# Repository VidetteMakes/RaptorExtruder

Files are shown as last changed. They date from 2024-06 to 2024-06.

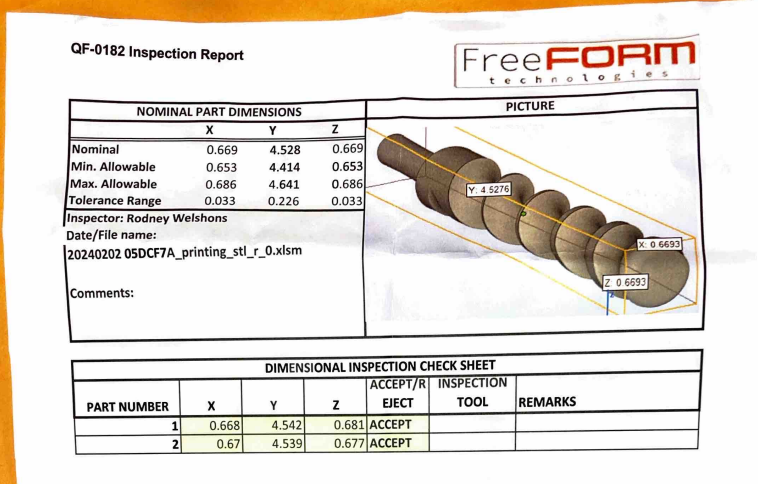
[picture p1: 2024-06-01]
CAD/Detailed/ExtrusionScrew Xometry Drawing.PNG

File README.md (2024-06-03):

# RaptorExtruder
Instructions to modify an Ender-3 3D printer to print from raw pellets

This pellet printing modification is designed to be open source, available to hobbyists for purchase and install. The pellet printer is able to bypass the manufacturing costs associated with filament printing, use flexible materials normally unsuitable for filament printing, and allow users to mix pellets for their own blends of printed material.

## Team
These fine Valparaiso University students worked for nine months to make this project happen:  [Blake Andrew](mailto:blake.andrew@valpo.edu), [Daniel Heinrich](mailto:daniel.heinrich@valpo.edu), [Mikey Pinchok](mailto:mikey.pinchok@valpo.edu), [Kay Shoolian](mailto:kay.shoolian@valpo.edu), [Ethan Storer](mailto:ethan.storer@valpo.edu), and [Timothy Ziemann](mailto:timothy.ziemann@valpo.edu).  Their team name was the "Vinyl Velocirapters."

Vidette Makes' [Adam Johnson](mailto:ajohnson@videttemakes.org) proposed the project and served as the team's "customer."

## Documentation
* [Design Document](https://github.com/VidetteMakes/RaptorExtruder/wiki/Design-Document)

## A Word from our Sponsor
Vidette Makes is a maker group in Valparaiso, Indiana, USA. We are a community of technical professionals, creatives, and enthusiasts working to build a shared workspace to enrich our city through meaningful educational and social projects. Our hope is that senior design projects like these can help improve education throughout our region, and benefit the open-source community.

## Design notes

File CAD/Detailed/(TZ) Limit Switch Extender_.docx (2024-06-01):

Timothy Ziemann

Limit Switch Extender

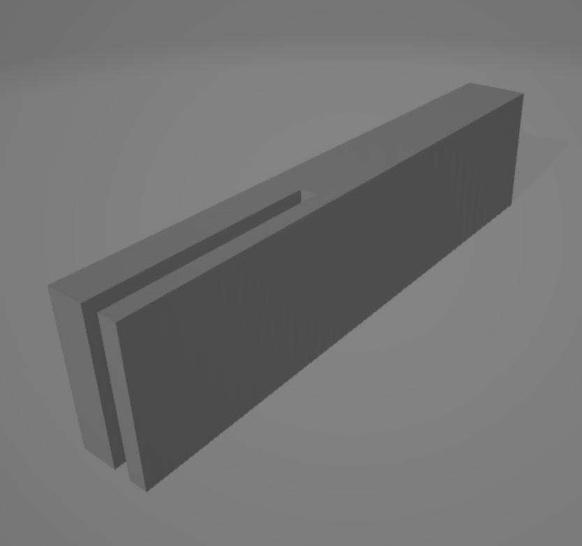
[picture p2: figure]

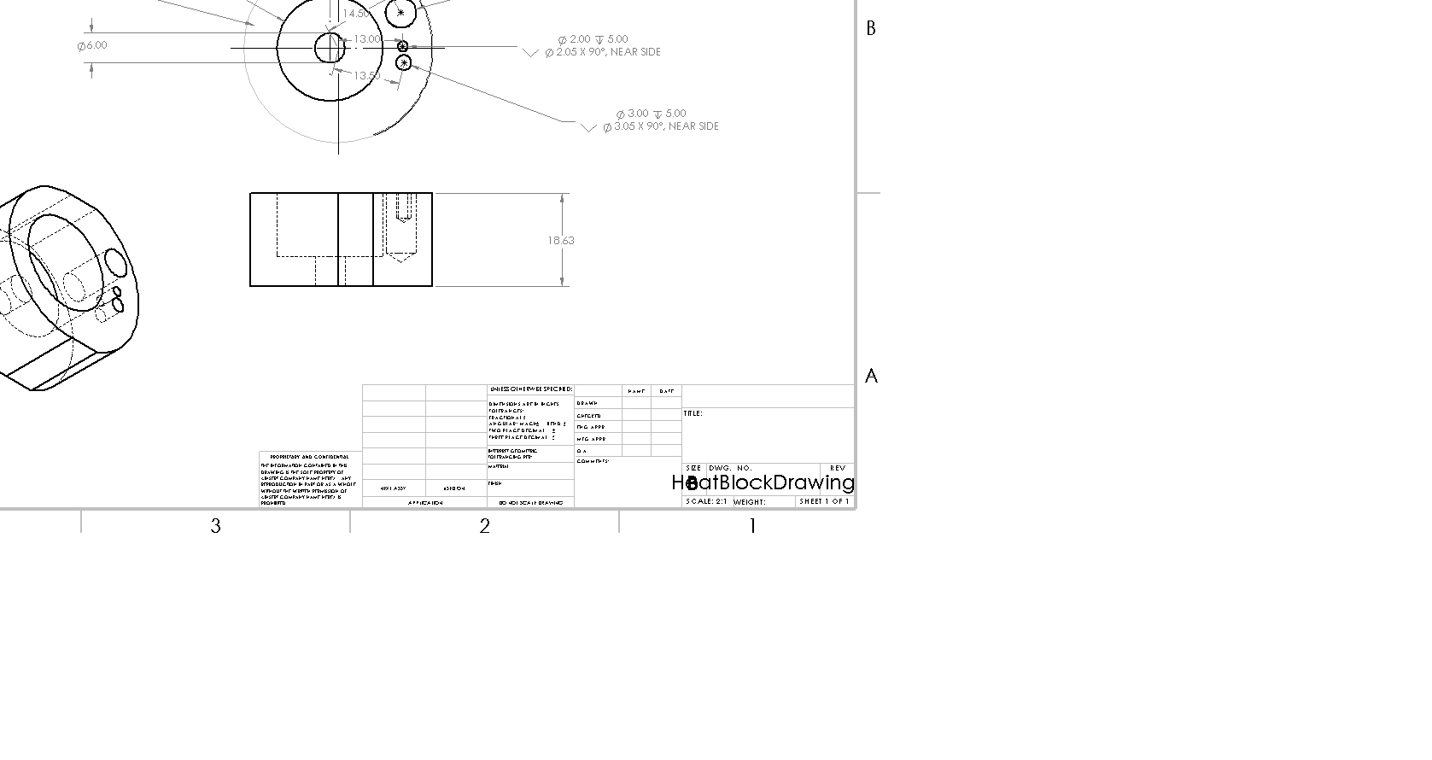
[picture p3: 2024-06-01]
CAD/Detailed/HeatBlockDrawing.JPG

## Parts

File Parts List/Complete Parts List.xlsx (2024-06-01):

Part Name | Part Number | Manufacturer | Supplier | Supplier number | Quantity | Unit per Cost | Shipping | Link | Total | 0.503902218
Central Teapot | 01 | 3D Printed | Onshape/Github Files | null | 1 | $2.82 | null | https://cad.onshape.com/documents/9373b47fd643172cff45d3d4/w/6b3f12529ad0d21ca0c2727d/e/8014758e9e8911c7f829dec0 | $196.25
Barrel Clamps | 02 | 3D Printed | Onshape/Github Files | null | 2 | $0.48 | null | https://cad.onshape.com/documents/d60d43ca9705b24c87fe40b2
Fan Bracket | 03 | 3D Printed | Onshape/Github Files | null | 1 | $0.34 | null | https://cad.onshape.com/documents/eff08e7556119b477b11b817
Extrusion Screw | 04 | Xometry | Onshape/Github Files | NA | 1 | $68.17 | FREE | https://cad.onshape.com/documents/d2be099d6e50864f19c8ab5b/w/c3f151076c51f3df40b7c22b/e/451508f13a050d7e0df22d9a
Barrel Drill Jig | 05 | 3D Printed | Onshape/Github Files | null | 1 | $0.18 | null | https://cad.onshape.com/documents/5ecc7b5bd6e7c801915e2fe7/w/c172fd17e7c9f8a495fd555d/e/54c839c322dd78154e47972e
Heat Block | 06 | Xometry | Onshape/Github Files | NA | 1 | $89.89 | FREE | https://cad.onshape.com/documents/1759477e29ceef14d57d62ff/w/edbe1dfc022f062bbb53088f/e/fbbaa3c68424f225d66270d6
Limit Switch Extension | 07 | 3D Printed | Onshape/Github Files | null | 1 | $1.83 | null | https://cad.onshape.com/documents/66e5bc53bb85858bbdae4f5e/w/fd5296b0bee12057fadcdff0/e/4f6b8865d1156799d3cb627d
O-ring Assortment (https://www.homedepot.com/p/Everbilt-Medium-Assorted-O-Ring-Kit-45-Pieces-866810/318763123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) | 08 | Everbilt | Home Depot | (219)531-6687 | 1 | $5.48 | null
Press Fit Shroud | 09 | 3D Printed | Onshape/Github Files | null | 1 | $0.08 | null | https://cad.onshape.com/documents/27f05f00ce109d2de31b7cee
1/2" x 11" Black Steel Nipple (https://www.homedepot.com/p/STZ-1-2-in-x-11-in-Black-Steel-Nipple-PDB-N12X11/316939836) | 12 | STZ | Home Depot | (219)531-6687 | 1 | $3.99 | null
8mm to 5mm coupler (https://www.amazon.com/Aluminium-Flexible-Coupling-Diameter-Connector/dp/B08JZ1D5BY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) | 85 | VI-CHAN | Amazon | null | 1 | $9.99 | FREE
Stepper Motor (https://www.amazon.com/Comgrow-Creality-Official-Stepper-Motor/dp/B09ZQT9DJY?th=1) | 00 | Creality | Amazon | 86 755 3396 5666 | 1 | $12.99 | FREE
10-32 x 3" Bolt | 10323 | null | Project Lab | null | 2 | null | null | null
10-32 x 2.5" Bolt | 103225 | null | Project Lab | null | 2 | null | null | null
10-32 x 2" Bolt | 10322 | null | Project Lab | null | 4 | null | null | null

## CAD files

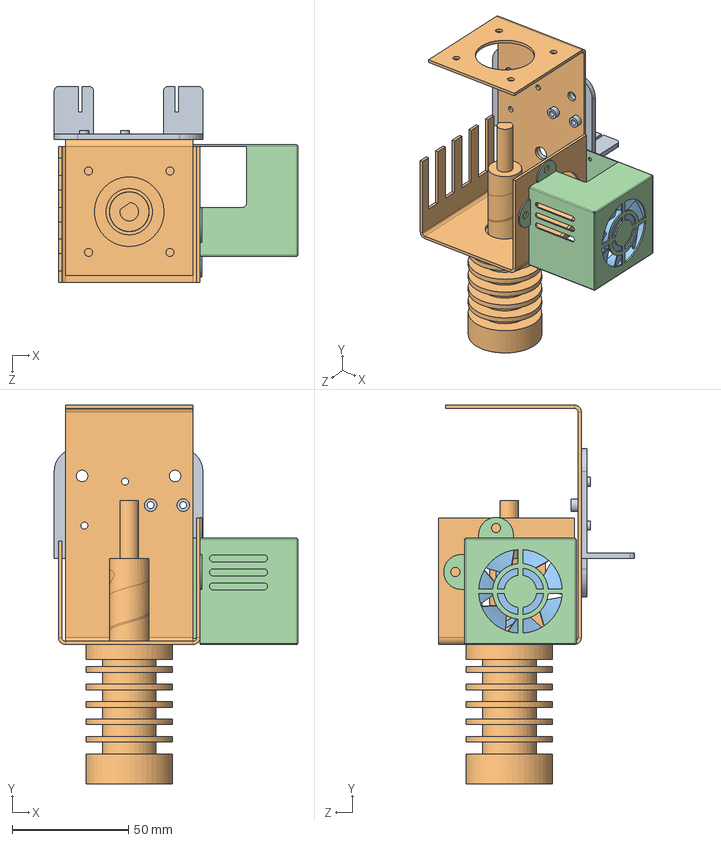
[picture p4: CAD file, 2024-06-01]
CAD/Assembly/HOTEND_ASSEM_KAY.SLDASM
104.8 x 163.0 x 84.4 mm
E plate
Storer_ExtrusionScrew x 4
Nozzle fan
Fan cover

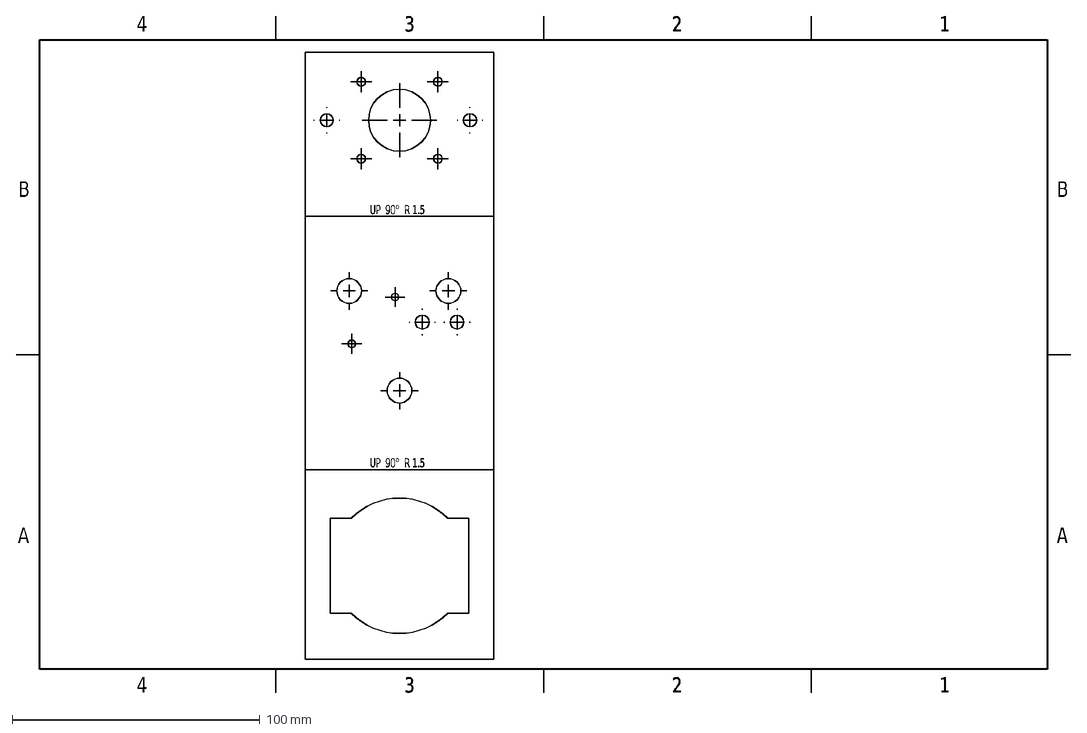
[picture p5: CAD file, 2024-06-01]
CAD/STL and DXF files/PLASMA_BRACKET_KS.DXF
A
B
4
3
2
1
UP 90° R 1.5

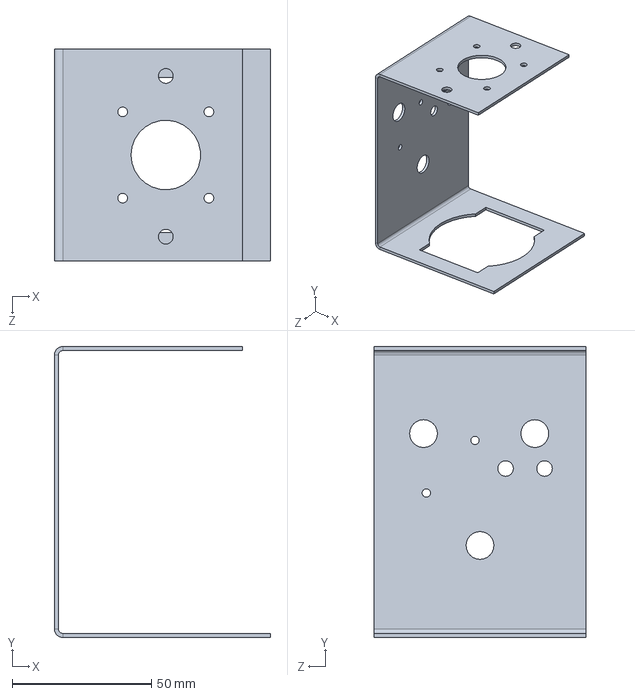
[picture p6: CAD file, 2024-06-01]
CAD/Detailed/PLASMA_BRACKET_KS.SLDPRT
77.7 x 104.6 x 76.2 mm

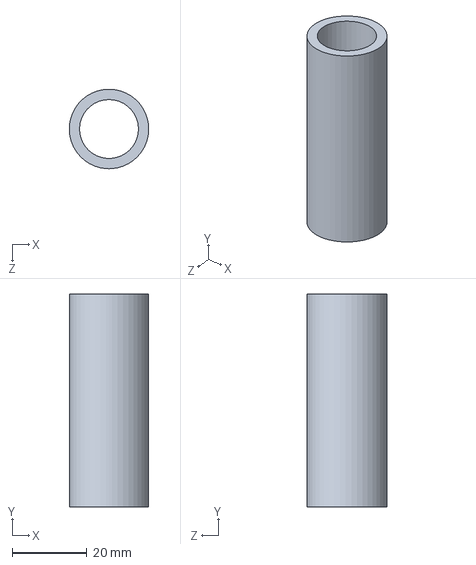
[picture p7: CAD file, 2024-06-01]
CAD/Detailed/KISS_Barrel.SLDPRT
21.3 x 57.1 x 21.3 mm

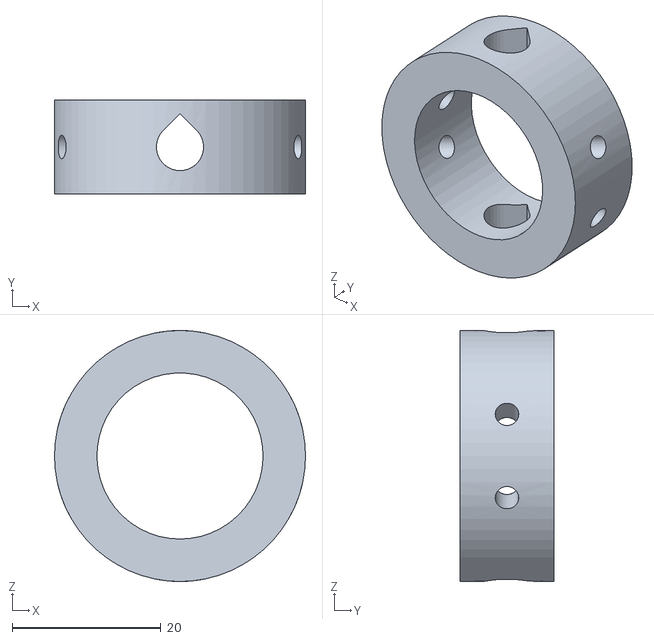
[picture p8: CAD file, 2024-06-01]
CAD/STL and DXF files/BarrelDrillJig.STL
33.8 x 12.7 x 33.8

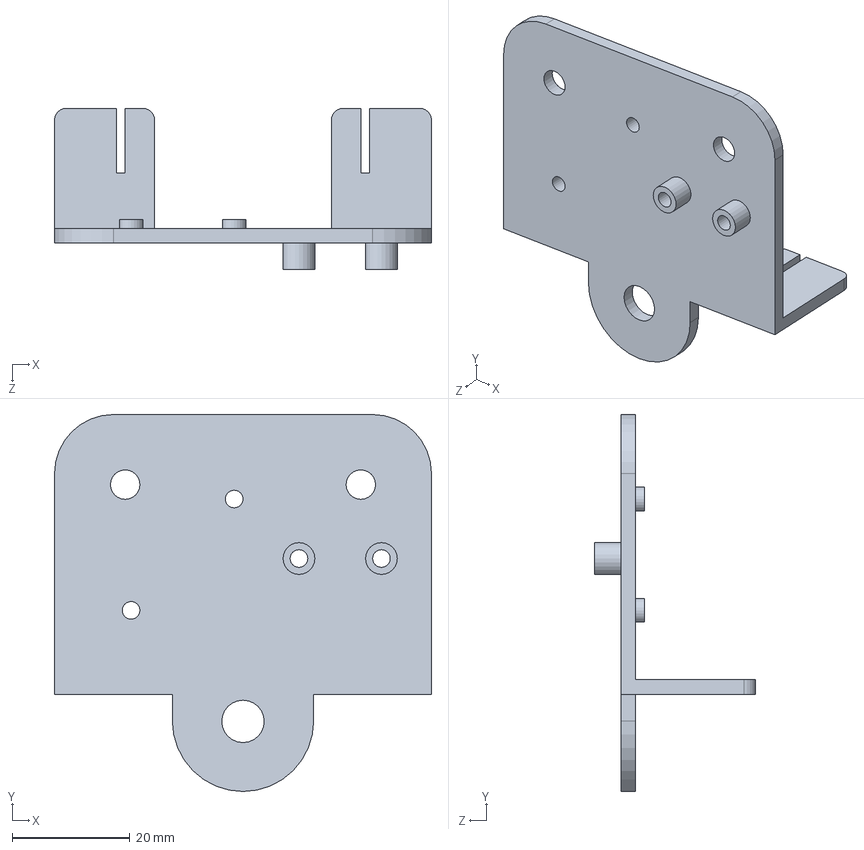
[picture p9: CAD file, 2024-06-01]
CAD/Detailed/E plate.SLDPRT
64.0 x 64.0 x 27.4 mm

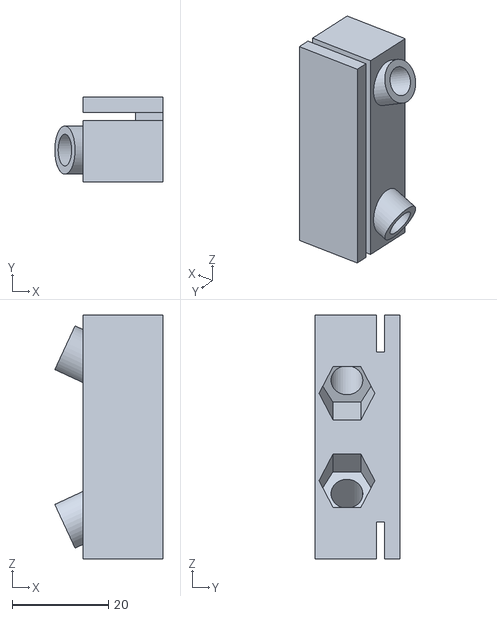
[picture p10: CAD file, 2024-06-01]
CAD/STL and DXF files/BARREL_CLAMPS_V2_KAY.STL
22.5 x 17.6 x 50.6

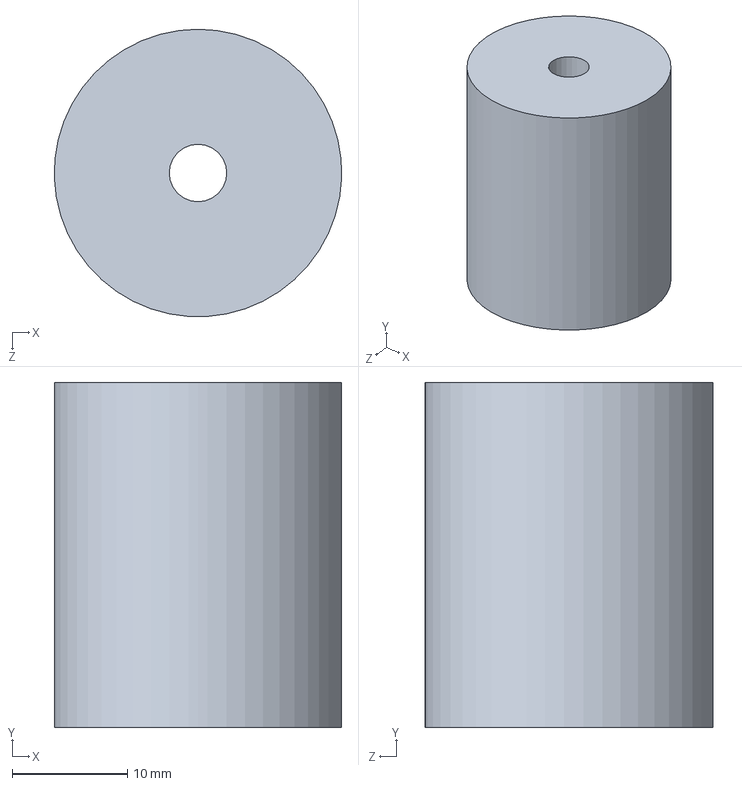
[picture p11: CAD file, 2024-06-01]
CAD/Detailed/COUPLER.SLDPRT
25.0 x 30.0 x 25.0 mm

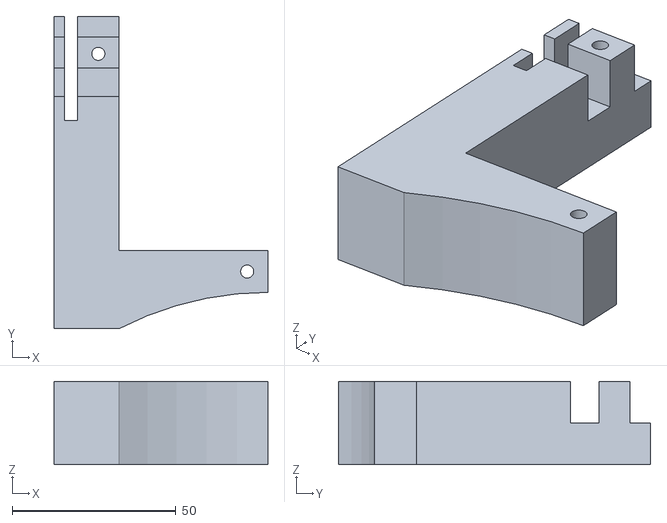
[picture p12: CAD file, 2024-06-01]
CAD/STL and DXF files/2.5in Limit Switch Extension.stl
65.3 x 95.2 x 25.4

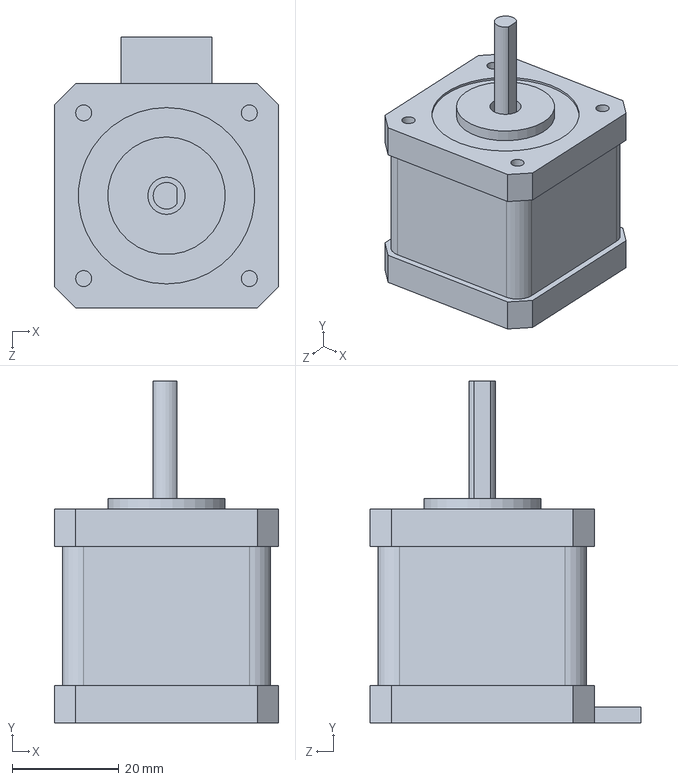
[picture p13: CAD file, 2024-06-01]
CAD/Detailed/42-40 motor.SLDPRT
42.0 x 64.0 x 50.7 mm

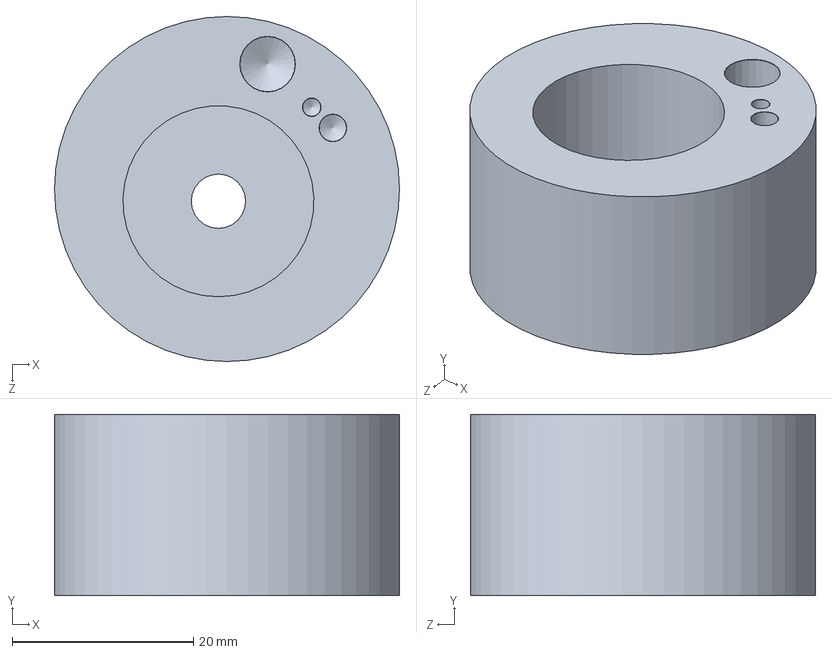
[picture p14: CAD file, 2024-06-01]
CAD/Detailed/Heat Block.SLDPRT
38.1 x 20.0 x 38.1 mm

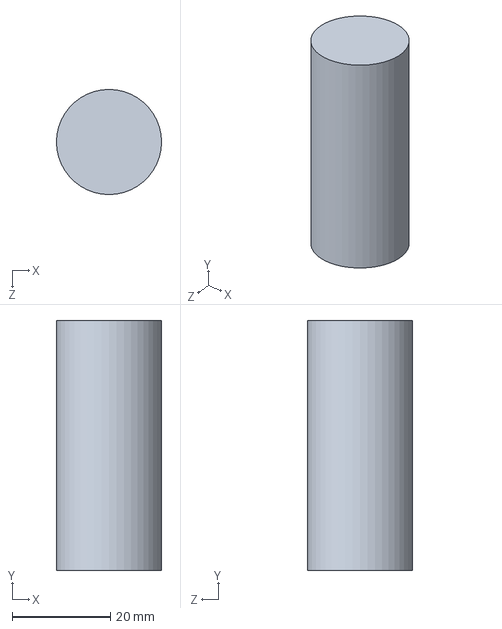
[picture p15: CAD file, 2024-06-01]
CAD/Detailed/SIMPLE_BARREL.SLDPRT
21.4 x 50.8 x 21.4 mm

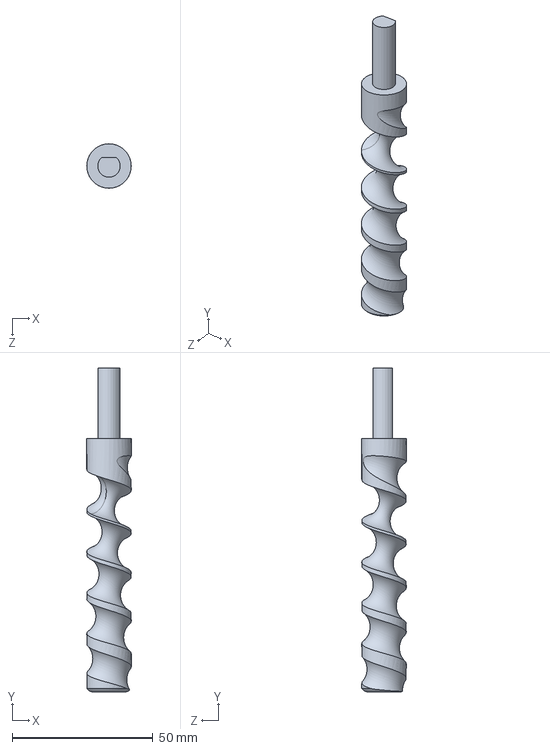
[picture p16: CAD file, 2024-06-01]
CAD/Detailed/Storer_ExtrusionScrew_TurnedDownV2.SLDPRT
15.8 x 115.0 x 15.8 mm

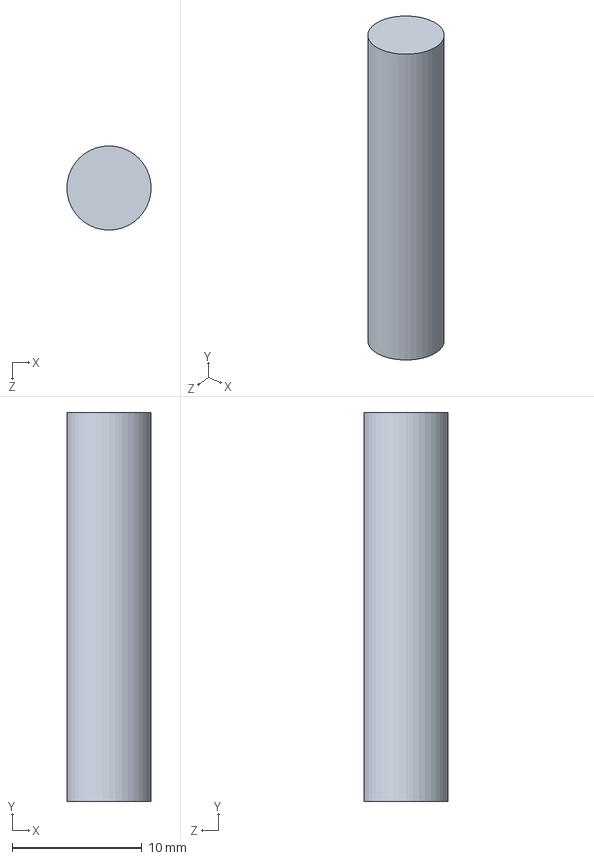
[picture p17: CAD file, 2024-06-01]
CAD/Detailed/TEST_SCREW.SLDPRT
6.50 x 30.0 x 6.50 mm

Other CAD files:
CAD/Detailed/BARREL_CLAMPS_V2_KAY.SLDPRT
CAD/Drawings/Heat Block.SLDDRW
CAD/Drawings/PLASMA_BRACKET_KS.SLDDRW

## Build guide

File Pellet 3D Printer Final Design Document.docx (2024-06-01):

Multidisciplinary Senior Design Projects

GE 498

College of Engineering

Valparaiso University

Valparaiso, Indiana

Design Document

For the

Pellet 3D Printer

Date: 05-06-2024

Prepared by: | Pellet 3D Printing (Vinyl Velociraptors)
Concurrence (Advisor): | Professor Luke
Concurrence (Advisor): | Professor El-Howayek
Approved (Customer):
Approved (Team Leader):

Total Number of Pages: 15

Executive Summary: This pellet printing modification is designed to be open source, available to hobbyists for purchase and install. The pellet printer is able to bypass the manufacturing costs associated with filament printing, use flexible materials normally unsuitable for filament printing, and allow users to mix pellets for their own blends of printed material.

Honor Code Statement

I have neither given or received, nor have I tolerated other’s use of unauthorized aid.

_________________________________________

Blake Andrew

_________________________________________

Daniel Heinrich

_________________________________________

Mikey Pinchok

_________________________________________

Kay Shoolian

_________________________________________

Ethan Storer

_________________________________________

Timothy Ziemann

Table of Contents

1 Introduction 4

2 System Description 4

2.1 Subsystem Description 4

3 Frequently Asked Questions (FAQ) 5

4 Design Problems and Solutions: 6

Likely Problems while Assembling the Extruder 6

5 Limitations and warnings 6

Warnings: 7

Limitations: 7

6 System Design Requirements 8

Using An Ender-3 Requirement 8

Assembly Instructions Requirements 8

Time Study Requirements 8

Performance Check Requirements 8

Size Requirements 8

Accessibility Requirements 9

6.2 Deviations from the System Design Requirements 9

7 Supporting Information 9

7.1 Referenced Documents 10

7.2 Symbols and Abbreviations 10

8 Distribution 10

Appendix A 11

Part List and Budget: 11

Appendix D, E, F 11

Detailed drawings illustrating for all manufactured components 11

Assembly drawings: 13

Flow Charts for Control Systems 14

Computer Code: 14

Electrical circuits: 14

Appendix G 15

## 1 Introduction

The goal of this project is to modify a stock Ender-3 3D printer to accept plastic pellets rather than filament and provide detailed documentation for hobbyists who want to replicate the design change.

## 2 System Description

Our system is a modified Ender 3 3D V1 printer. It is modified to utilize plastic pellets as a printing material instead of plastic filament. This modification would make the 3D print more environmentally friendly and cheaper with use of pellets over processed filament rolls. The other main goal is to make this project and modification open source. This will provide repeatable instructions for hobbyists to modify their printers at home through following an assembly guide with steps, parts, and a time study. This design report aims to walk through our problem definition, system overview, virtual prototype, and finalized budget. Our team (The Vinyl Velociraptors) have been working on these four categories for the last 10 months and this document will be a compilation of the data and product we have made.

## 2.1 Subsystem Description

The system begins with a hopper connected to the central mounting teapot via a corrugated tube. It is mounted atop the Ender 3 V2’s gantry.

The central mounting teapot houses the barrel, hotend, fans, extrusion screw, and the stepper motor that turns the extrusion screw. It is printed on the stock Ender 3 3D printer. This component also houses the barrel mounting system. There are two 3D printed barrel clamps which secure the barrel and allow for precise adjustment of it. These can be printed by the unmodified 3D printer. The part fan and barrel fan are also a part of this system and are crucial to keeping the system at the proper temperature.

The extrusion screw utilizes a logarithmic design to build pressure to push out plastic for printing. It is purchased from Xometry.

The barrel is a pipe that can be purchased from a hardware store. It is cut to size and press fit into the heater block using a vice.

The hot end contains the heat stock Ender 3 heat cartridge, chosen for its ease of implementation and compatibility with the existing Ender 3 heat cartridge and thermistor which are also utilized for our system. This heater block also contains a 0.6mm nozzle which can be purchased from Creality. The hotend and barrel subsystem is crucial for transforming pellets into molten material, ready for extrusion through the nozzle.

A extrusion screw bit, inserted into the hotend barrel, is driven by a stepper motor. This motor has a built in 5:1 gearbox and is connected to the extrusion screw bit through a coupler. The extrusion screw and geared stepper motor ensures a controlled and consistent feeding of pellets into the hotend barrel, contributing to the overall accuracy and reliability of the 3D printing process.

The system is seamlessly integrated with the Ender 3 V2's software, allowing users to control the pellet feeding process, temperature settings, and other parameters. Ender software integration ensures user-friendly control of the 3D printing process, making it accessible to experienced and novice users.

## 3 Frequently Asked Questions (FAQ)

Q: What is the estimated cost of making this printer modification?

A: Assuming you don’t have access to a machine shop, the total comes out to be around $200

Q: Where can I buy plastic pellets?

A: Pellets can be purchased in bulk from online stores like 3DxTech, we got our polypropylene (PP) pellets from techkits.com (https://www.techkits.com/products/resin-ppnat/) because it was a much smaller quantity.

Q: How much does using pellets save compared to filament?

A: Pellets can be around 50% cheaper compared to filament. Depends on the quality of the filament and the size of the pellet order.

Q: Does this work with new versions of the Ender 3D printer?

A: Theoretically yes, although the mounting holes may be different. Nothing involved in the printing process is tied to the Ender-3 V1 specifically.

Q: How fast can this printer modification print?

A: We set it to print at 6.5mm/s for testing purposes, but likely could have printed faster. A lot of the speed limitations came down to the extra weight of the modified extruder.

Q: What slicer software did you use to make the custom settings for the pellet printer?

A: Prusa Slicer is our slicer of choice, but it is by no means the only option.

## 4 Design Problems and Solutions:

- Partially melted plastic pellets leaking through the o-ring at the interface of the “teapot” and the barrel
  - Solution was to improve the installation of the o-ring and install a new/better teapot. O-ring no longer acts as a thermal bridge
- Teapot would become partially melted the longer the printer remained hot.
  - O-ring was installed better and no longer acts as a thermal bridge
  - An additional fan was added to provide convection cooling to the top of the barrel
- Pressure created by screw during operation would deform the bracket
  - Bracket was replaced with a 3D printed teapot to provide improved rigidity.
- Screws that adjust the barrel position in the bracket do not provide adequate pressure to hold it in place.
  - Shallow blind holes can be drilled into the barrel to allow for better hold.

### Likely Problems while Assembling the Extruder

- Printer is beeping loudly
  - Thermistor is likely improperly installed or damaged. Inspect the thermistor and reseat it. If the printer continues to beep, ensure that none of the fans are blowing on it directly. If none of these fixes the beeping, consider replacing the thermistor. Also consider adding Kapton Tape (https://www.amazon.com/ELEGOO-Polyimide-Temperature-Resistant-Multi-Sized/dp/B072Z92QZ2?hvadid=616931741728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) around the heat block for improved installation. Another option to insulate the barrel if the Kapton Tape is not sufficient is the use of fiberglass insulation, like that from exhaust wrap.
- 3D prints are messy
  - Ensure you are using the provided print configurations.
- 3D prints won’t stick to the bed
  - Ensure your bed is hot enough for your choice of plastic.
  - Clean the bed using isopropyl alcohol to ensure there is no plastic residue.
  - If using Polypropylene, ensure that the bed is covered in packing tape, and that the bed heat is upwards of 80 degrees celsius.
- Packing tape is lifting off of the bed
  - While still printing, tape down the lifting sections with more packing tape

## 5 Limitations and warnings

- While using the teapot in either PETG or ABS materials, the teapot will melt if it is not set to the proper temperature and cooling levels.
  - If this becomes a constant issue, a teapot printed from a higher temperature glass transition point material such as Nylon 11 in an SLS printer can negate those problems
  - An insulative fiberglass board cut to add insulation below the teapot can reduce the heat transfer into the teapot.
    - Cheaply by hand and stencil with a pre purchased board
    - Using a laser cutting service such as sendcutsend
- While the printer is believed to be capable of printing in materials other than polypropylene, this has not been officially tested
  - Be aware of the temperature of both the teapot and especially the barrel brackets to ensure all components remain solid

### Warnings:

- Printer gets very hot, do not touch it during operation. Furthermore, ensure no flammable materials are near the printer while operating.
- Inspect your thermistor before installation to ensure that it is working properly. This reduces the risk of thermal runaway.
- It is not recommended to run a 3D printer without a person nearby in case something goes wrong
- Modify your printer at your own risk, we cannot guarantee the safety of any modifications done to the printer.
- Print in a well ventilated area to reduce the risk of toxic gasses building up, especially while using plastics like ABS or TPU

### Limitations:

- Printer cannot retract plastic while printing, leading to extra strings in the print while z-hopping.
- We don’t have an efficient way to purge old plastic while changing materials or colors
- The build height of the printer has been reduced by the increased size of the pellet extruder system.
- The print speed of the printer has been reduced by the increased weight of the pellet extruder system.
- The printer has a very limited maximum temperature of about 210°C - 220 °C. The firmware expects to see a certain amount of temperature change for some amount of power that gets dumped into the heat block. Since the heat block is much larger than the stock Ender-3 block, or any other heat block out there, it loses heat very quickly and trips the “Heating Failed” error very easily. Note that hotter temperatures will cause the printer to bleed off heat more quickly!

## 6 System Design Requirements

### Using An Ender-3 Requirement

1.1 The system shall modify an existing Ender-3 3D printer

1.2 The system shall use PP pellets instead of filament to create 3D printed objects.

1.3 The system may accept ABS, PLA, PETG and TPU pellets instead of filament.

1.4 The system shall not interfere with the safety features of the Ender-3.

### Assembly Instructions Requirements

2.1 The instructions shall describe the requirements to install the pellet modification.

2.2 The instructions shall be a highschool graduate reading level.

2.3 The instructions shall include pictures with a step by step format for building the device.

### Time Study Requirements

3.1 The construction process shall be documented and completed 3 times.

3.2 The system shall take less than 5 hours to construct for an individual who is not familiar with the design.

### Performance Check Requirements

4.1 There shall be no more than a ±5% difference in dimensions between a calibration cube printed by the system and a stock Ender-3.

4.2 There shall be no more than a ±5% difference in weight of a calibration cube printed by the system and a stock Ender-3.

### Size Requirements

5.1 The system shall fit in a 3 ft by 3 ft by 3ft cube space.

5.2 The extruder system shall weigh less than 3 pounds

### Accessibility Requirements

6.1 The system shall use widely available or simple pre-designed parts.

6.2 The materials necessary to make the modification shall cost less than $350.

6.3 The system shall avoid melting/grinding/cutting to make parts fit.

6.4 The system shall only use tools that most hobbyists have easy access to.

6.5 If there is a specialty item, its place of purchase shall be documented.

6.6 The system shall use fasteners, not glue.

6.7 The system shall use connectors whenever possible, not solder, to minimize failure of electronic components.

6.8 Any part requiring special skills (welding, soldering, or machining) to construct or assemble shall be quoted from at least three vendors, and justified by the team in a meeting to ensure it fits within the total budget.

## 6.2 Deviations from the System Design Requirements

4.1 The dimensional deviations between the stock Ender and our modification was on average ±8%

4.2 The polypropylene material we used for pellet printing is unavailable in filament form, meaning we were unable to test this requirement.

6.1 The core of the system uses a custom metal 3D printed logarithmic screw, which is neither simple nor widely available.

6.4 Some parts of the system such as the heater block had to be machined.

## 7 Supporting Information

### 7.1 Referenced Documents

US20160347000A1.pdf (https://drive.google.com/file/d/1btAa_Q-sDPHqLyyBR-ihErtMZL8ppcnh/view?usp=drive_link)

polymers-13-03353.pdf (https://drive.google.com/file/d/1Sh1UzTP04CTPRqTO__MObnyoIkQHghQI/view?usp=drive_link)

s40964-019-00088-4.pdf (https://drive.google.com/file/d/16hsIs7RPbFy4fzcSIrZV6rPczBE_E7Sp/view?usp=drive_link)

### 7.2 Symbols and Abbreviations

ABS - Acrylonitrile Butadiene Styrene

TPU - Thermoplastic polyurethane

PP - Polypropylene

## 8 Distribution

Original.......... Team Leader
1 copy............. Primary Advisor
1 copy............. Course Coordinator

## Appendix A

### Part List and Budget:

- Complete Parts List (https://docs.google.com/spreadsheets/d/110W6ZweZZwfarbQIxILViImiIQHg95aWJ4IGoY0l1n8/edit)

## Appendix D, E, F

### Detailed drawings illustrating for all manufactured components

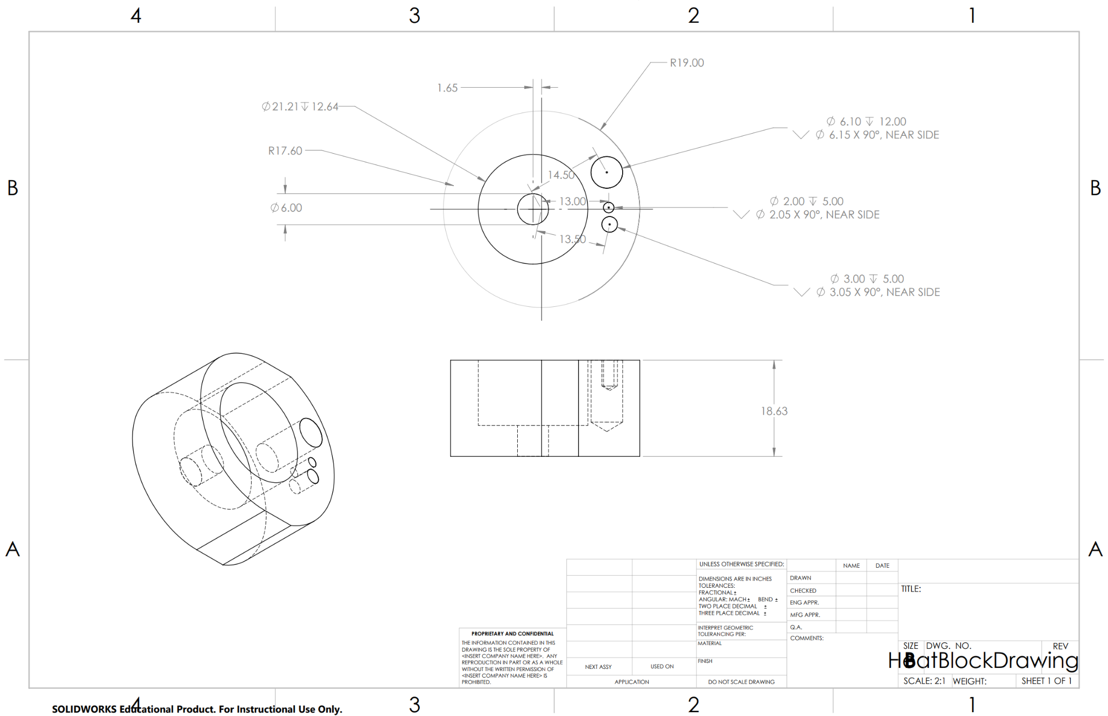
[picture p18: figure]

The flat edges are not necessary in the final design as they were originally meant for making the part more manufacturable. The barrel’s most important dimension is the press-fit hole for the black steel barrel. The dimensions for the three smaller holes follow the hole pattern spacing for the Ender-3 heat block very closely.

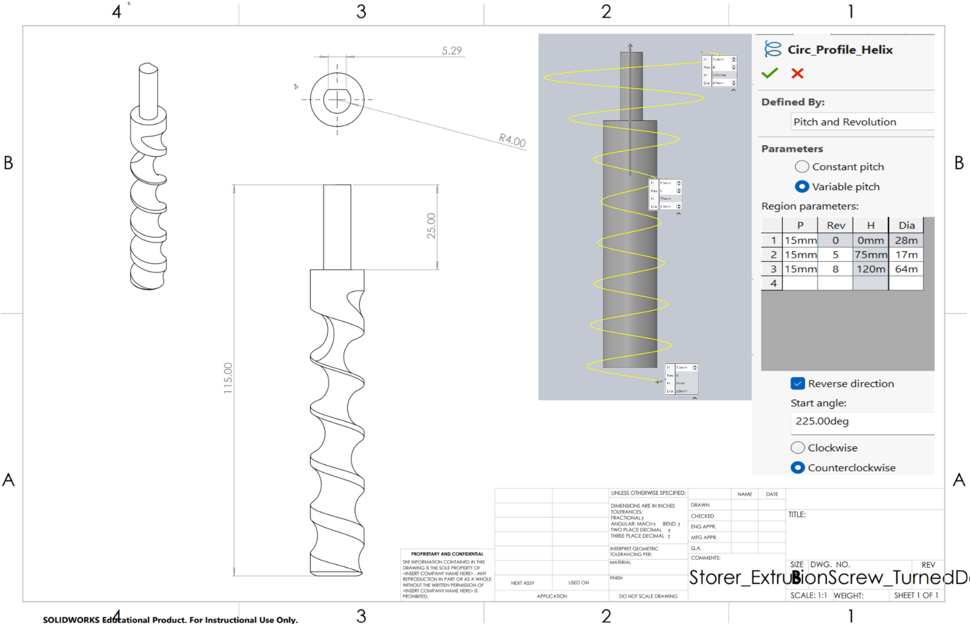
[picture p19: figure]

The screw’s geometry is based on a helix with three individual segments with their own pitch. The parameters for the helices are labeled on the preview with three little boxes. The parameters for the helices are also in the Circ_Profile_Helix table.

### Assembly drawings:

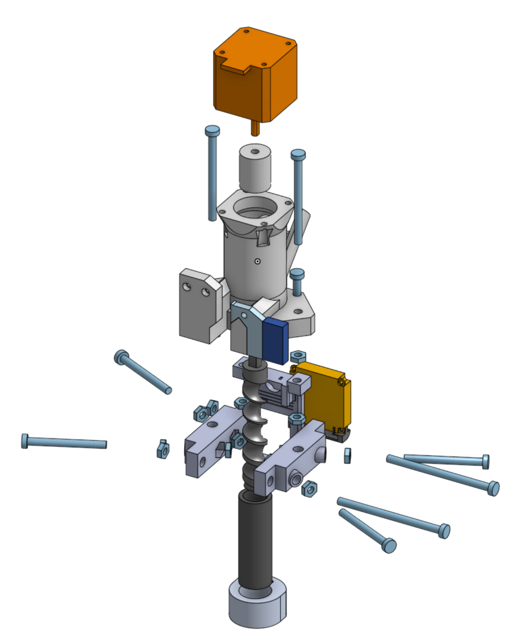
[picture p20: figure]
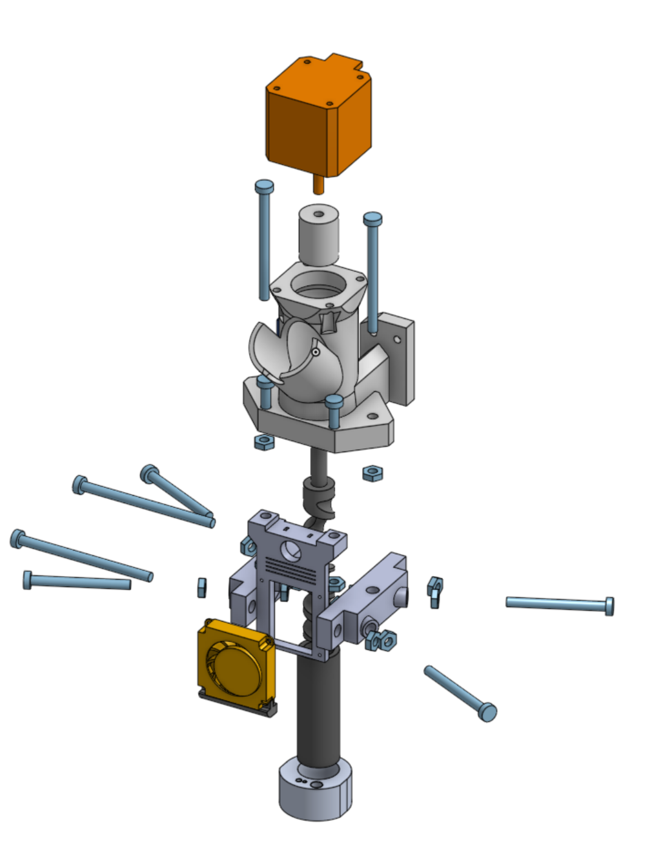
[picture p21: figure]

Two isometric views of the exploded model. The model and its parts can be found in the OnShape Project Folder (https://cad.onshape.com/documents/24ec814f0aa771ba6b6b39f4/w/7c7ef0db674f39f2ce4eb73b/e/5d7ee87e87f6b38be38cb68a).

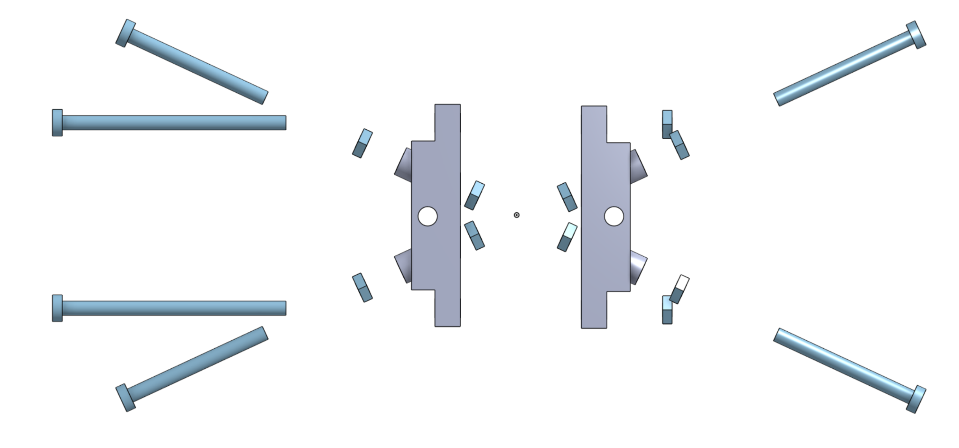
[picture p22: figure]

Isolated view of the barrel clamps and the bolts.

### Flow Charts for Control Systems

- We did not write our own control systems since the Ender 3 had built in control systems.

### Computer Code:

- We did not write code for the operation of the system, but did write code to calculate the dimensions of the screw. Those calculations are linked below.
  - Computer Codes (https://drive.google.com/drive/folders/1YNIQtn1I4rh5Mel5AXPEYvcBOearV0iV?usp=drive_link)

### Electrical circuits:

- The electrical circuits included in the Ender 3 are shown below. Besides that, we did not design any electrical circuits as the ender had all the control systems required.
  - Circuit Diagrams (https://drive.google.com/drive/folders/1OTnrep8ZZs7Rkf0-R4wiGuxogoQwrrbr?usp=drive_link)
  - The Ender Circuit provides all the control circuitry for powering the fans and sending signals to the stepper motors.
  - The stepper motor circuitry was used for our project specifically to reverse the direction of the stepper motor rotation. Such circuitry won’t be needed for future iterations of this design, as the screw will be designed correctly to extrude while spinning in the default Ender 3 “forward” direction.

## Appendix G

Pellet 3D Printer Assembly Instructions (https://docs.google.com/document/d/1HU0jos_mn8zzjRmjtwaB9pEYKUADIomTM53ebHeet08/edit)

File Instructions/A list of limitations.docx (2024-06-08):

A list of limitations

1. What materials can you print with?

We have only printed with polypropylene, however it should be possible to print with other materials such as PLA or ABS. Printing with PETG pellets might be difficult since all the 3D printed parts are made out of PETG. The customer should try materials with a lower melting temperature lower than PETG’s before experimenting with PETG pellets.

2. What print speed can you use?

Here is ai list of adjusted settings that we were able to adjust in the Ender 3 panel.

- Speed: 100 → 65
- Acceleration: 500 → 375
- Jerk VX and VY: 8 → 6
- Fan Speed: 5%

The print speed is significantly slower than a stock Ender 3. A stepper motor with agearbox could result in faster sprint speeds.

3. What flow rate can you use?

The flow was also adjusted in the panel from 100 → 50. This setting changes how fast the extruder spins when extruding. It was necessary to lower the flower, in order to achieve more torque since our stepper motor doesn’t have gearbox. However, the lowered flow doesn’t affect the printing speed by much since the extrusion screw creates an immense amount of pressure

4. What are the capabilities of the printer?

Presenting a benchy shows that the pellet 3D printer is capable of even complex geometries. The accuracy has to be improved but we showed that retraction is possible. The retraction speed must be lowered in the slicer settings however.

5. Duration of a print?

Due to lowered print speeds, the duration of a benchy print was roughly doubled from around 1.5 hours to 3 hours. Hence, expect roughly a doubled print time.

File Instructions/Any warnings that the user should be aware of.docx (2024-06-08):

Any warnings that the user should be aware of

1. Heat
  a. As with any other 3D printer, the hot end will have some very hot components. Our design includes a much larger heater block, which can be even more dangerous. Never touch the metal components until the printer is thoroughly cooled down.
  b. In our current design, we are using the extruder stepper motor to spin our extrusion screw. We recommend a stepper motor with a gearbox for future iterations since the current stepper motor can get extremely hot during a print longer than an hour or two.
2. Longevity
  a. We only extruded polypropylene with a relatively low melting temperature during our testing processes. Thus, printing with PLA or PETG pellets, which require a hotter heater block, can cause the 3D-printed parts to melt. If you see parts such as the teapot and clamps melting, turn off the printer immediately and reprint the parts. To prevent further melting the fan speeds must be adjusted accordingly.
3. Gloves and masks are necessary when working with fiberglass.
  a. When insulation is necessary, it is essential to wear gloves and masks when working with fiberglass and, ideally, work in open spaces. Keep it away from children and handle it with care.

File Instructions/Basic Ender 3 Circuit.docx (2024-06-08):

Creality Ender-3 V2 3D printer

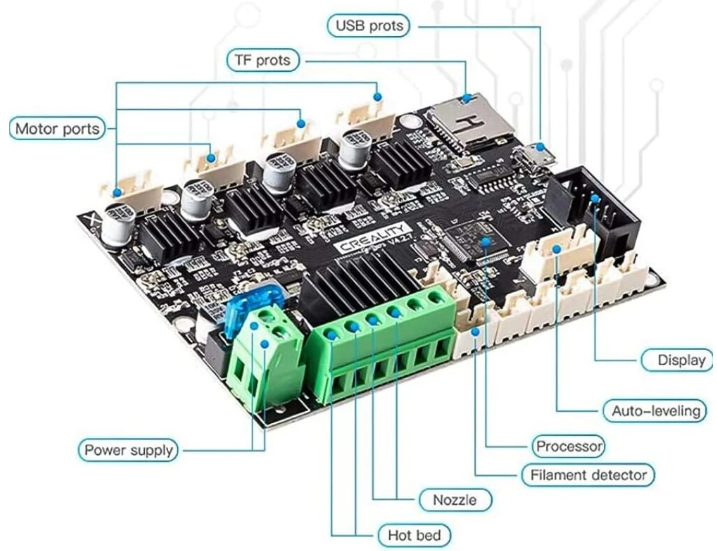
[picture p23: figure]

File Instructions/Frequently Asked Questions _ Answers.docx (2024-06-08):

Frequently Asked Questions / Answers

1. Why is a pellet 3D printer better?

Printing out of pellets is more environmentally friendly and cheaper since the extrusion process to make filament is skipped.

2. How long would it take to modify my printer?

Modifying your printer is a breeze. If you print all 3D parts overnight and deliver custom-machined parts, you can expect to have your modification assembled in just an afternoon. It's a quick and efficient process that puts you in control of your 3D printing setup.

3. What was the biggest struggle in designing the system?

Heat management thermal runaway was a significant issue during our design process. Isolating the thermistor with glass fiber solved that problem.

4. How many of the parts are custom vs off the shelf?

Even though our design ended up with more custom parts than off-the-shelf parts, our custom parts are easily accessible by providing necessary STL and CAD files. The ½ inch steel pipe is the only off-the-shelf part of our design.

5. How much money would it take to modify my printer?

The modification would cost around $250, with the heater block being the most expensive part since it is CNC-machined.

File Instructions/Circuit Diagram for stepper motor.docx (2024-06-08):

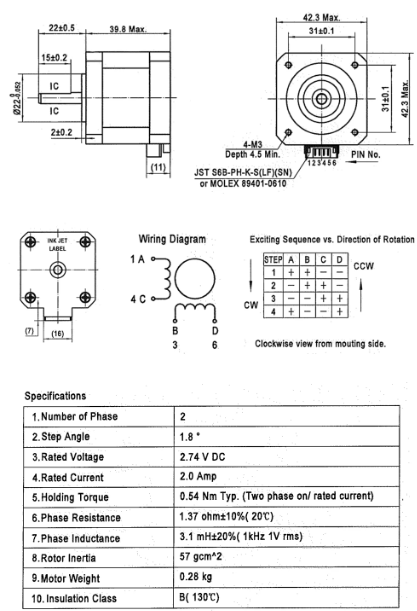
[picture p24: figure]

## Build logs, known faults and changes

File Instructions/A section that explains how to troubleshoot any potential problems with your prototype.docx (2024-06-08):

A section that explains how to troubleshoot any potential problems with your prototype

Potential troubleshooting:

Extrusion Stepper Motor Stalling:

If the stepper motor stalls even though the heater block is at temperature, take control and try extruding manually to see if it stalls. Adjust the fan speed if necessary, which may prevent the pellets from melting at the top of the barrel. Increasing the temperature of the heater block could also solve the problem. However, at the moment, we don’t recommend a higher temperature than 210°C.

Thermistor freaking out:

During our testing, the thermistor detected thermal runaway many times. Due to a very large heater block, the slightest forced convection can cause thermal runaway. We solved this by completely isolating the thermistor with a layer of kapton-wrapped glass fiber. To eliminate this step, we recommend a screw-in thermistor for the next iteration.

When your prints have consistent ripples:

This is known as z-wobbling, which can also happen on a filament printer, but since our printhead is much heavier than the stock, it amplifies the effect.

Potential solutions:

- Cleaning the z-axis lead screw.
- Make sure couplers are tight enough or not too tight.

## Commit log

2024-05-31 Update README.md
    Added CAD naming convention.
2024-06-01 Added CAD, BOM, instruction manual, project proposal, and final team report.
    [2.5in Limit Switch Extension.stl, 42-40 motor.SLDPRT, BARREL_CLAMPS_V2_KAY.SLDPRT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]
2024-06-08 Folder rename for clarity
    [Complete Parts List.xlsx]
2024-06-08 Added pellet size analysis.
    [Pellet Size Analysis.xlsx]
